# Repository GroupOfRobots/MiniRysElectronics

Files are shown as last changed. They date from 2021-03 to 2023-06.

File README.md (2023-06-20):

# MiniRysElectronics
This repo contains schematics and PCB layouts for all the custom boards used by the MiniRyś robot.

supervisor: Kamil Jabłoński

Boards:
* RysBoard
* RysBattery
* beacon (obsolete)
* dwm1000_addon (obsolete)

## RysBoard
Main board for the MiniRyś robot - a Raspberry Pi 4B shield with motor drivers, power delivery circuitry, sensor connectors and more.

## RysBattery
Custom 18650 battery holder supporting protected cells (longer!) and with reverse polarity protection.

## Beacon
(obsolete)

A STM Nucleo adapter for the DWM1000 module with a power input jack.

## DWM1000 addon
(obsolete)

A DWM1000 module breakout board that was to be compatible with both the RysBoard and the Beacon boards.

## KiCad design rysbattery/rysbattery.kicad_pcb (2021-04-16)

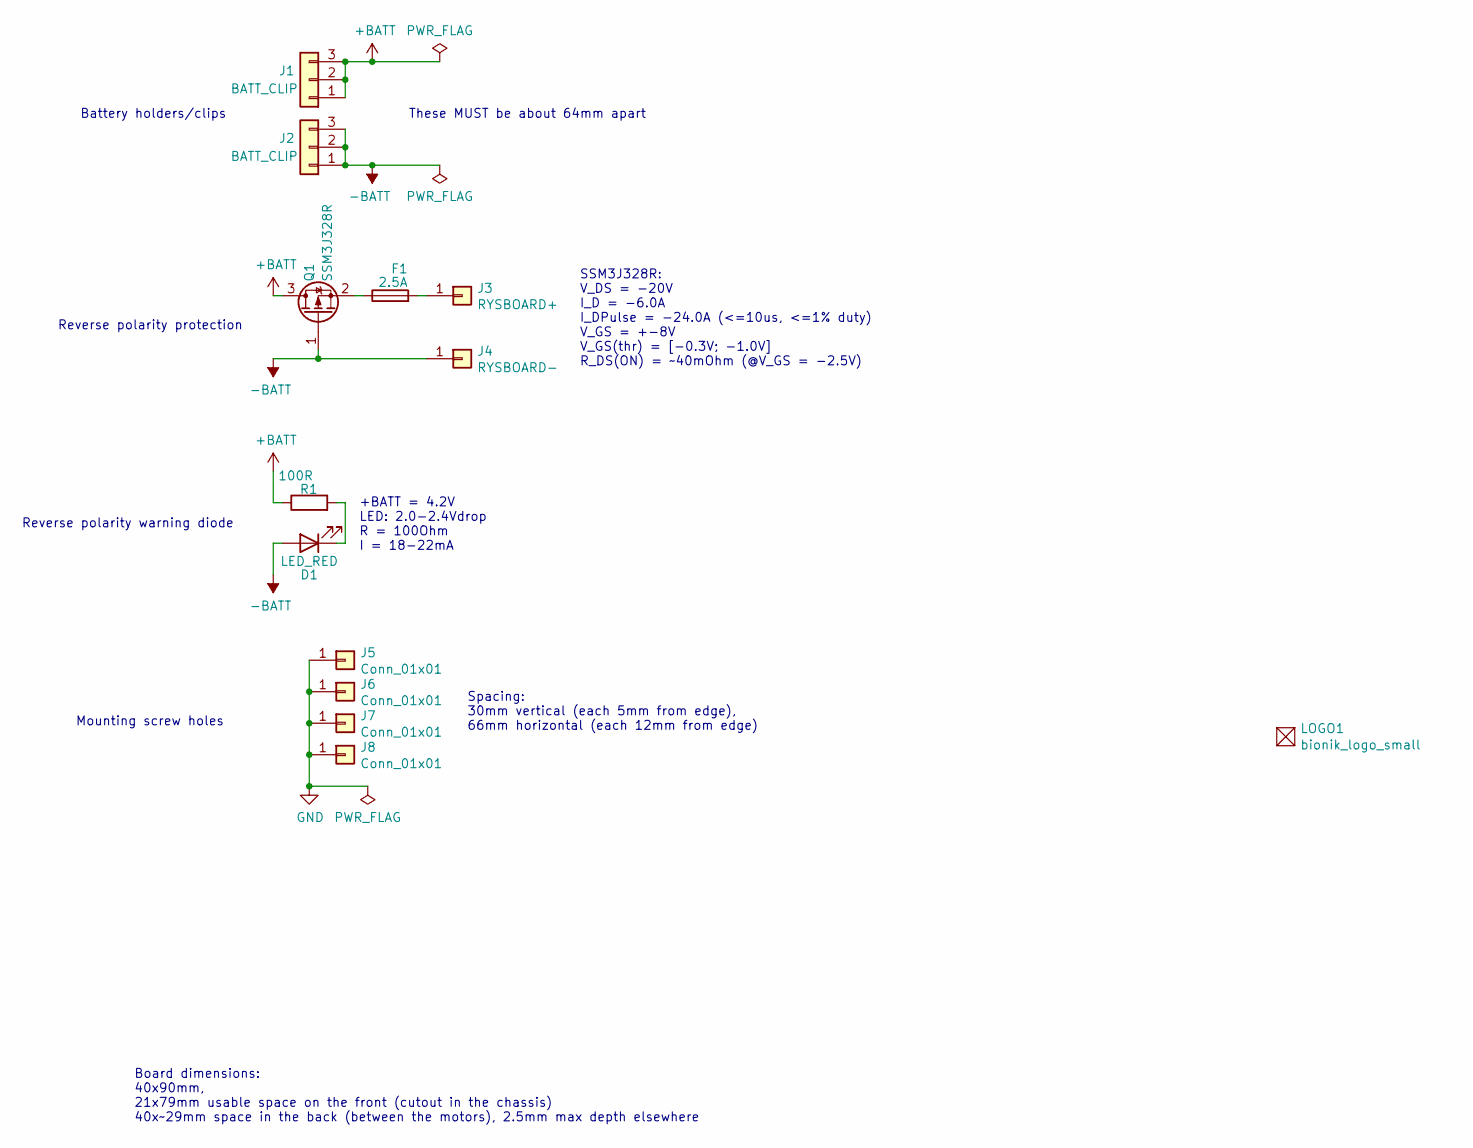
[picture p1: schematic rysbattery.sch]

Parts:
D1: LED_RED; LED_0805_2012Metric_Pad1.15x1.40mm_HandSolder
F1: 2.5A; Fuse_1206_3216Metric_Pad1.42x1.75mm_HandSolder
J1, J2: BATT_CLIP; keystone_54
J3: RYSBOARD+; SolderWire-0.75sqmm_1x01_D1.25mm_OD2.3mm_Relief
J4: RYSBOARD-; SolderWire-0.75sqmm_1x01_D1.25mm_OD2.3mm_Relief
J5, J6, J7, J8: Conn_01x01; MountingHole_3.2mm_M3_DIN965_Pad
LOGO1: bionik_logo_small
Q1: SSM3J328R; SOT-23_Handsoldering
R1: 100R; R_0603_1608Metric_Pad1.05x0.95mm_HandSolder

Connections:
+BATT: J1.1, J1.2, J1.3, Q1.3 (D), R1.1
-BATT: D1.2 (A), J2.1, J2.2, J2.3, J4.1, Q1.1 (G)
GND: J5.1, J6.1, J7.1, J8.1
unnamed: D1.1 (K), R1.2
unnamed: F1.1, Q1.2 (S)
unnamed: F1.2, J3.1

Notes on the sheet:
Reverse polarity warning diode
+BATT = 4.2V LED: 2.0-2.4Vdrop R = 100Ohm I = 18-22mA
Battery holders/clips
These MUST be about 64mm apart
Reverse polarity protection
Mounting screw holes
SSM3J328R: V_DS = -20V I_D = -6.0A I_DPulse = -24.0A (<=10us, <=1% duty) V_GS = +-8V V_GS(thr) = [-0.3V; -1.0V] R_DS(ON) = ~~40mOhm (@V_GS = -2.5V)
Spacing: 30mm vertical (each 5mm from edge), 66mm horizontal (each 12mm from edge)
Board dimensions: 40x90mm, 21x79mm usable space on the front (cutout in the chassis) 40x~~29mm space in the back (between the motors), 2.5mm max depth elsewhere

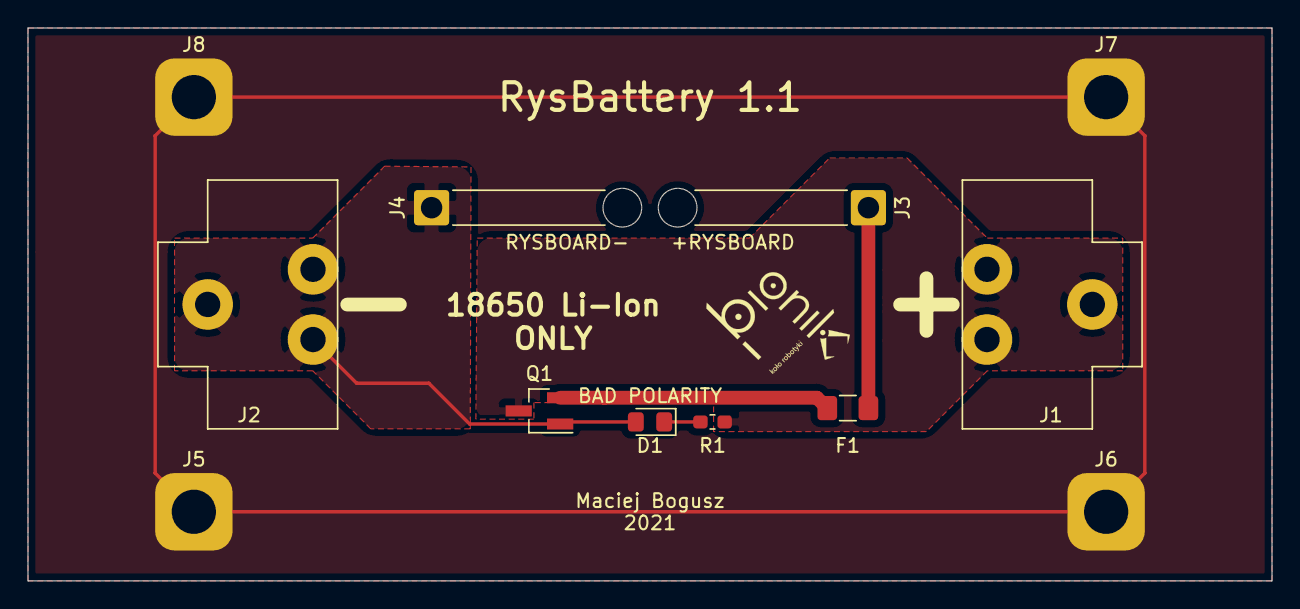
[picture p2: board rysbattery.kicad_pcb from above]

Board: 2 copper layers, 90.0 x 40.0 mm, 13 parts (0 on the bottom side), 6 nets.

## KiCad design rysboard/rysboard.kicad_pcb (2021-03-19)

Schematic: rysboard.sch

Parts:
D6: GREEN; LED_0805_2012Metric
D7: RED; LED_0805_2012Metric
D10: 1N4148; D_0603_1608Metric
H1, H2, H3, H4: MountingHole_Pad; MountingHole_2.7mm_M2.5_Pad
J1: RPi4; PinSocket_2x20_P2.54mm_Vertical
J17: Conn_01x03; PinHeader_1x03_P2.54mm_Vertical
J18: Conn_01x02; PinHeader_1x02_P2.54mm_Vertical
LOGO1: bionik_logo
Q1: BC847BS; SOT-363_SC-70-6
Q2: BC817; SOT-23
R7, R10: 10k; R_0603_1608Metric
R11, R12, R15: 680R; R_0603_1608Metric

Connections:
+3V3: J1.1 (3V3), J1.17 (3V3); also elsewhere on the board
+5V: D10.1, J1.2 (5V), J1.4 (5V), J18.2, R11.2, R12.1; also elsewhere on the board
/FAN_PWM: J1.12 (GPIO18/PWM0), R15.1
/I2C1_SCL: J1.5 (SCL/GPIO3); also elsewhere on the board
/I2C1_SDA: J1.3 (SDA/GPIO2); also elsewhere on the board
/I2C3_SCL: J1.29 (GCLK1/GPIO5); also elsewhere on the board
/I2C3_SDA: J1.7 (GCLK0/GPIO4); also elsewhere on the board
/I2C5_SCL: J1.33 (PWM1/GPIO13); also elsewhere on the board
/I2C5_SDA: J1.32 (PWM0/GPIO12); also elsewhere on the board
/LED1: J1.16 (GPIO23), R10.2
/LED2: J1.18 (GPIO24), R7.2
/MOTOR_BUSY: J1.13 (GPIO27); also elsewhere on the board
/MOTOR_FLAG: J1.11 (GPIO17); also elsewhere on the board
/SPI_CLK: J1.23 (SCLK0/GPIO11); also elsewhere on the board
/SPI_IRQEXT: J1.22 (GPIO25); also elsewhere on the board
/SPI_MISO: J1.21 (MISO0/GPIO9); also elsewhere on the board
/SPI_MOSI: J1.19 (MOSI0/GPIO10); also elsewhere on the board
/TOF1_EN: J1.31 (GCLK2/GPIO6); also elsewhere on the board
/TOF2_EN: J1.36 (GPIO16); also elsewhere on the board
/TOF3_EN: J1.35 (GPIO19/MISO1); also elsewhere on the board
/TOF4_EN: J1.38 (GPIO20/MOSI1); also elsewhere on the board
/TOF5_EN: J1.40 (GPIO21/SCLK1); also elsewhere on the board
/TOF6_EN: J1.37 (GPIO26); also elsewhere on the board
/UART_RXD: J1.10 (GPIO15/RXD), J17.3
/UART_TXD: J1.8 (GPIO14/TXD), J17.2
/~MOTOR_STBY: J1.15 (GPIO22); also elsewhere on the board
/~SPI_CS0: J1.24 (~CE0~/GPIO8); also elsewhere on the board
/~SPI_CS1: J1.26 (~CE1~/GPIO7); also elsewhere on the board
GND: H1.1, H2.1, H3.1, H4.1, J1.6 (GND), J1.9 (GND), J1.14 (GND), J1.20 (GND), J1.25 (GND), J1.30 (GND), J1.39 (GND), J17.1, Q1.1, Q1.4, Q2.2; also elsewhere on the board
unnamed: D6.1 (K), Q1.3
unnamed: D6.2 (A), R11.1
unnamed: D7.1 (K), Q1.6
unnamed: D7.2 (A), R12.2
unnamed: D10.2, J18.1, Q2.3
unnamed: Q1.2, R10.1
unnamed: Q1.5, R7.1
unnamed: Q2.1, R15.2

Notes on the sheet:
Raspberry Pi 4 connector
Status LEDs
UART connector
Raspberry Pi 4 mounting holes (GND)
I2C Note: RPi4 has internal pull-ups for I2C-1 bus and the ToF sensor boards used have a set of pull-ups each for their respective buses (I2C-3 and -5); Therefore no additional pullups are required
Cooling Fan

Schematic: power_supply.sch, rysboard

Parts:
C15, C18, C22: 100n; C_0603_1608Metric
C16, C17, C20, C21: 10u; C_1206_3216Metric
C19: 10n; C_0603_1608Metric
D3: RED; LED_0805_2012Metric
D4, D9: GREEN; LED_0805_2012Metric
D5, D8: SK52; D_SMB
F1: 2.5A; Fuse_1206_3216Metric
J4: CELL3; Molex_Micro-Fit_3.0_43045-0212_2x01_P3.00mm_Vertical
J5: CELL2; Molex_Micro-Fit_3.0_43045-0212_2x01_P3.00mm_Vertical
J6: CELL1; Molex_Micro-Fit_3.0_43045-0212_2x01_P3.00mm_Vertical
J7: SW; Molex_Micro-Fit_3.0_43045-0212_2x01_P3.00mm_Vertical
L1: 3.3uH; L_6.7x6.7_H2.2
R8, R9, R25: 10k; R_0603_1608Metric
R13: 110k1%; R_0603_1608Metric
R14: 21k1%; R_0603_1608Metric
R19: 15k1%; R_0603_1608Metric
R20, R22, R24: 10k1%; R_0603_1608Metric
R21: 36k1%; R_0603_1608Metric
R23: 56k1%; R_0603_1608Metric
R27: 680R; R_0603_1608Metric
U3: ST1S10; TI_SO-PowerPAD-8; PartID ST1S10PHR
U4: MAX11613; 8-uMAX; PartID MAX11613EUA+

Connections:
+3V3: C15.1, U4.8; also elsewhere on the board
+5V: C19.1, C20.1, C21.1, C22.1, D8.1 (K), D9.2 (A), R13.2; also elsewhere on the board
/I2C1_SCL: U4.5; also elsewhere on the board
/I2C1_SDA: U4.6; also elsewhere on the board
/Power Supply/V_CELL1: J5.1, J6.2, R19.1
/Power Supply/V_CELL2: J4.1, J5.2, R21.1
/Power Supply/V_CELL3: F1.2, J4.2, R8.2, R23.1
GND: C15.2, C16.2, C17.2, C18.2, C19.2, C20.2, C21.2, C22.2, J7.1, R9.2, R14.2, R20.1, R22.1, R24.1, R25.1, R27.2, U3.4 (AGND), U3.5 (SYNC), U3.8 (PGND), U3.9 (PADGND), U4.7; also elsewhere on the board
unnamed: D3.1 (K), D4.2 (A), D5.2 (A), F1.1
unnamed: D3.2 (A), R8.1
unnamed: D4.1 (K), R9.1
unnamed: D8.2 (A), L1.2
unnamed: D9.1 (K), R27.1
unnamed: J6.1, J7.2
unnamed: L1.1, U3.7 (SW)
unnamed: R13.1, R14.1, U3.3 (FB)
unnamed: R19.2, R20.2, U4.1
unnamed: R21.2, R22.2, U4.2
unnamed: R23.2, R24.2, U4.3
unnamed: R25.2, U4.4
Vdrive: C16.1, C17.1, C18.1, D5.1 (K), U3.1 (VINA), U3.2 (INH), U3.6 (VINSW); also elsewhere on the board

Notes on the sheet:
Step-down converter
I2C ADC
V_CELL1: 3.0 - 4.2V -> Div 2.5 V_CELL2: 6.0 - 8.4V -> Div 4.5 V_CELL3: 9.0 - 12.6V -> Div 6.5 V_REF: 2.048V
V_out = V_FB * (1 + R13/R14) R13 = R14 x (V_out - V_FB) / V_FB V_out ~= 5.0V V_FB = 0.8V (typ); +-24mV R14 = 21k & R13 = 110k -> V_out = 4.99V

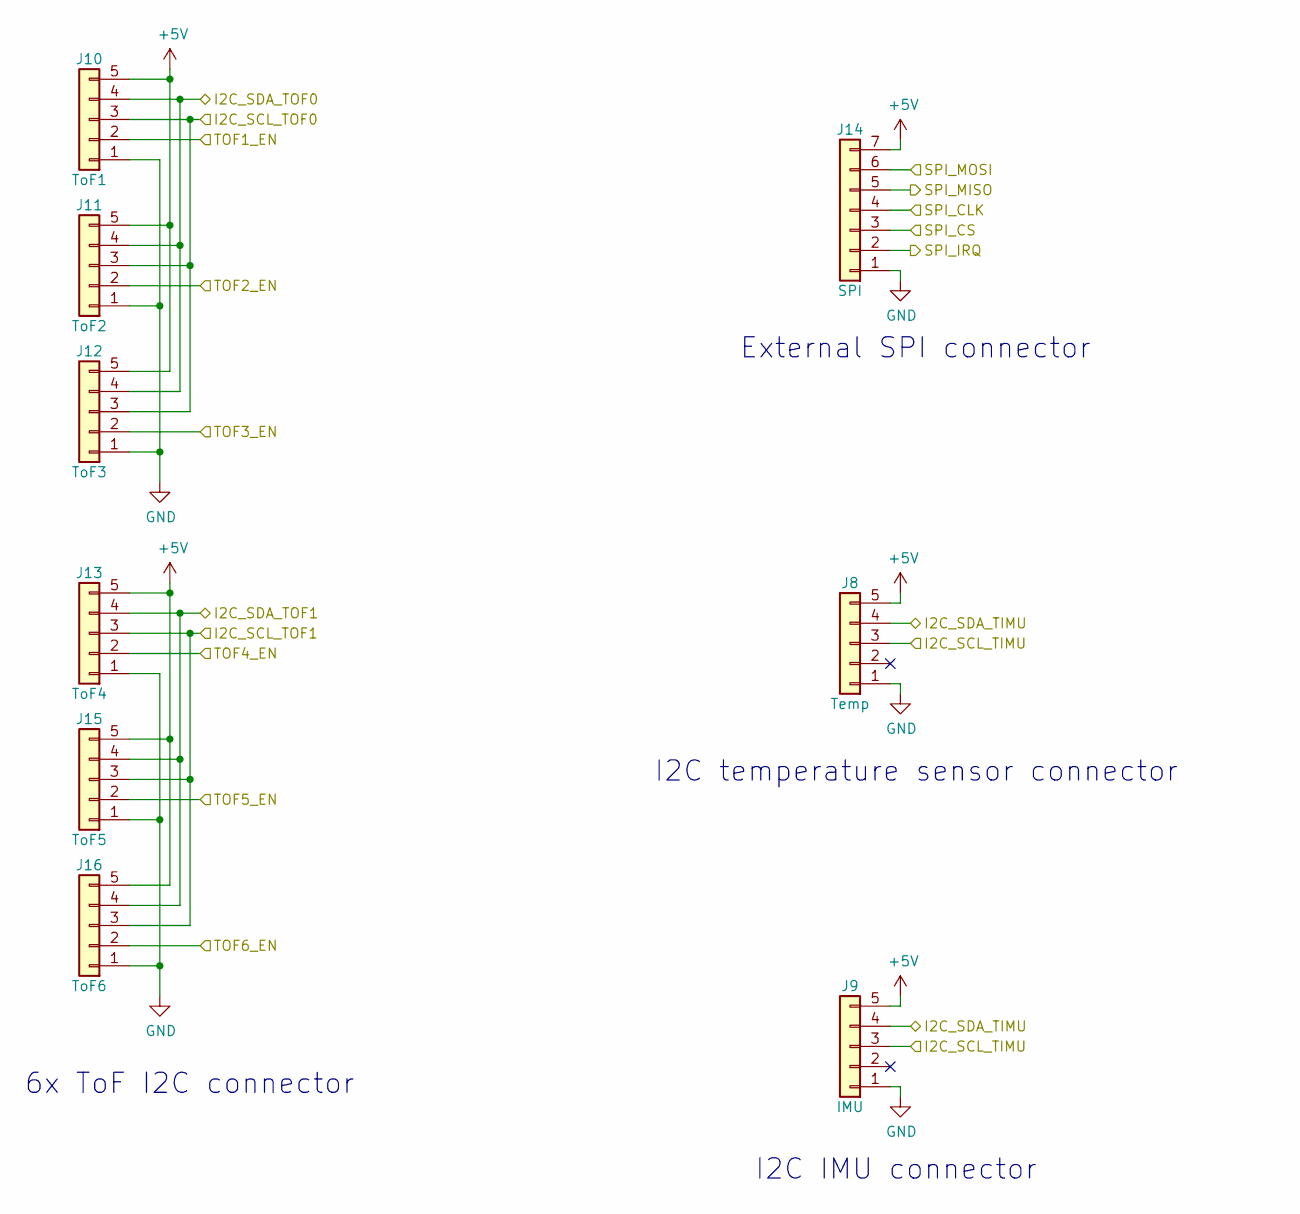
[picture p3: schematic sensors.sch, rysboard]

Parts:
J8: Temp; Molex_PicoBlade_53047-0510_1x05_P1.25mm_Vertical
J9: IMU; Molex_PicoBlade_53047-0510_1x05_P1.25mm_Vertical
J10: ToF1; Molex_PicoBlade_53047-0510_1x05_P1.25mm_Vertical
J11: ToF2; Molex_PicoBlade_53047-0510_1x05_P1.25mm_Vertical
J12: ToF3; Molex_PicoBlade_53047-0510_1x05_P1.25mm_Vertical
J13: ToF4; Molex_PicoBlade_53047-0510_1x05_P1.25mm_Vertical
J14: SPI; Molex_PicoBlade_53047-0710_1x07_P1.25mm_Vertical
J15: ToF5; Molex_PicoBlade_53047-0510_1x05_P1.25mm_Vertical
J16: ToF6; Molex_PicoBlade_53047-0510_1x05_P1.25mm_Vertical

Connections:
+5V: J8.5, J9.5, J10.5, J11.5, J12.5, J13.5, J14.7, J15.5, J16.5; also elsewhere on the board
/I2C1_SCL: J8.3, J9.3; also elsewhere on the board
/I2C1_SDA: J8.4, J9.4; also elsewhere on the board
/I2C3_SCL: J10.3, J11.3, J12.3; also elsewhere on the board
/I2C3_SDA: J10.4, J11.4, J12.4; also elsewhere on the board
/I2C5_SCL: J13.3, J15.3, J16.3; also elsewhere on the board
/I2C5_SDA: J13.4, J15.4, J16.4; also elsewhere on the board
/SPI_CLK: J14.4; also elsewhere on the board
/SPI_IRQEXT: J14.2; also elsewhere on the board
/SPI_MISO: J14.5; also elsewhere on the board
/SPI_MOSI: J14.6; also elsewhere on the board
/TOF1_EN: J10.2; also elsewhere on the board
/TOF2_EN: J11.2; also elsewhere on the board
/TOF3_EN: J12.2; also elsewhere on the board
/TOF4_EN: J13.2; also elsewhere on the board
/TOF5_EN: J15.2; also elsewhere on the board
/TOF6_EN: J16.2; also elsewhere on the board
/~SPI_CS1: J14.3; also elsewhere on the board
GND: J8.1, J9.1, J10.1, J11.1, J12.1, J13.1, J14.1, J15.1, J16.1; also elsewhere on the board

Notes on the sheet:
External SPI connector
I2C temperature sensor connector
6x ToF I2C connector
I2C IMU connector

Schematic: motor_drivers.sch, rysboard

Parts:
C1, C8: 10u; C_1206_3216Metric
C2, C9: 220n; C_0805_2012Metric
C3, C10: 10n; C_0603_1608Metric
C4, C7, C11, C14: 100n; C_0603_1608Metric
C5, C6, C12, C13: 47u; CP_EIA-7343-31_Kemet-D
D1, D2: BAV99; SOT-23
J2: Motor L; Molex_Micro-Fit_3.0_43650-0415_1x04_P3.00mm_Vertical
J3: Motor R; Molex_Micro-Fit_3.0_43650-0415_1x04_P3.00mm_Vertical
R1, R2, R26: 10k; R_0603_1608Metric
R3, R5: 27k1%; R_0603_1608Metric
R4, R6: 10k1%; R_0603_1608Metric
U1, U2: L6470; HTSSOP-28-1EP_4.4x9.7mm_P0.65mm_EP3.4x9.5mm_ThermalVias

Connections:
+3V3: C1.1, C4.1, C8.1, C11.1, R1.1, R2.1, R26.1, U1.4 (SW), U1.6 (VREG), U1.17 (VDD), U2.4 (SW), U2.6 (VREG), U2.17 (VDD); also elsewhere on the board
/Motor Drivers/SPI_BRIDGE: U1.18 (SDO), U2.20 (SDI)
/Motor Drivers/~BUSY_1: R2.2, U1.22 (~BUSY~/SYNC); also elsewhere on the board
/Motor Drivers/~BUSY_2: R26.2, U2.22 (~BUSY~/SYNC); also elsewhere on the board
/Motor Drivers/~FLAG_1: U1.24 (~FLAG); also elsewhere on the board
/Motor Drivers/~FLAG_2: U2.24 (~FLAG); also elsewhere on the board
/SPI_CLK: U1.19 (SCLK), U2.19 (SCLK); also elsewhere on the board
/SPI_MISO: U2.18 (SDO); also elsewhere on the board
/SPI_MOSI: U1.20 (SDI); also elsewhere on the board
/~MOTOR_STBY: R1.2, U1.3 (~STBY~/~RST), U2.3 (~STBY~/~RST); also elsewhere on the board
/~SPI_CS0: U1.23 (~CS), U2.23 (~CS); also elsewhere on the board
GND: C1.2, C4.2, C5.2, C6.2, C7.2, C8.2, C11.2, C12.2, C13.2, C14.2, R4.2, R6.2, U1.9 (AGND), U1.13 (PGND), U1.21 (DGND), U1.27 (PGND), U1.29 (GND), U2.9 (AGND), U2.13 (PGND), U2.21 (DGND), U2.27 (PGND), U2.29 (GND); also elsewhere on the board
unnamed: C2.2, D1.2 (A), U1.11 (VBOOT)
unnamed: C3.1, D1.3 (K)
unnamed: C3.2, U1.10 (CP)
unnamed: C9.2, D2.2 (A), U2.11 (VBOOT)
unnamed: C10.1, D2.3 (K)
unnamed: C10.2, U2.10 (CP)
unnamed: J2.1, U1.28 (OUT2A)
unnamed: J2.2, U1.1 (OUT1A)
unnamed: J2.3, U1.14 (OUT1B)
unnamed: J2.4, U1.15 (OUT2B)
unnamed: J3.1, U2.28 (OUT2A)
unnamed: J3.2, U2.1 (OUT1A)
unnamed: J3.3, U2.14 (OUT1B)
unnamed: J3.4, U2.15 (OUT2B)
unnamed: R3.2, R4.1, U1.5 (ADCIN)
unnamed: R5.2, R6.1, U2.5 (ADCIN)
Vdrive: C2.1, C5.1, C6.1, C7.1, C9.1, C12.1, C13.1, C14.1, D1.1 (K), D2.1 (K), R3.1, R5.1, U1.2 (VSA), U1.12 (VSB), U1.16 (VSB), U1.26 (VSA), U2.2 (VSA), U2.12 (VSB), U2.16 (VSB), U2.26 (VSA); also elsewhere on the board

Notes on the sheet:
Pull-ups for STANDBY and BUSY flags (active low)

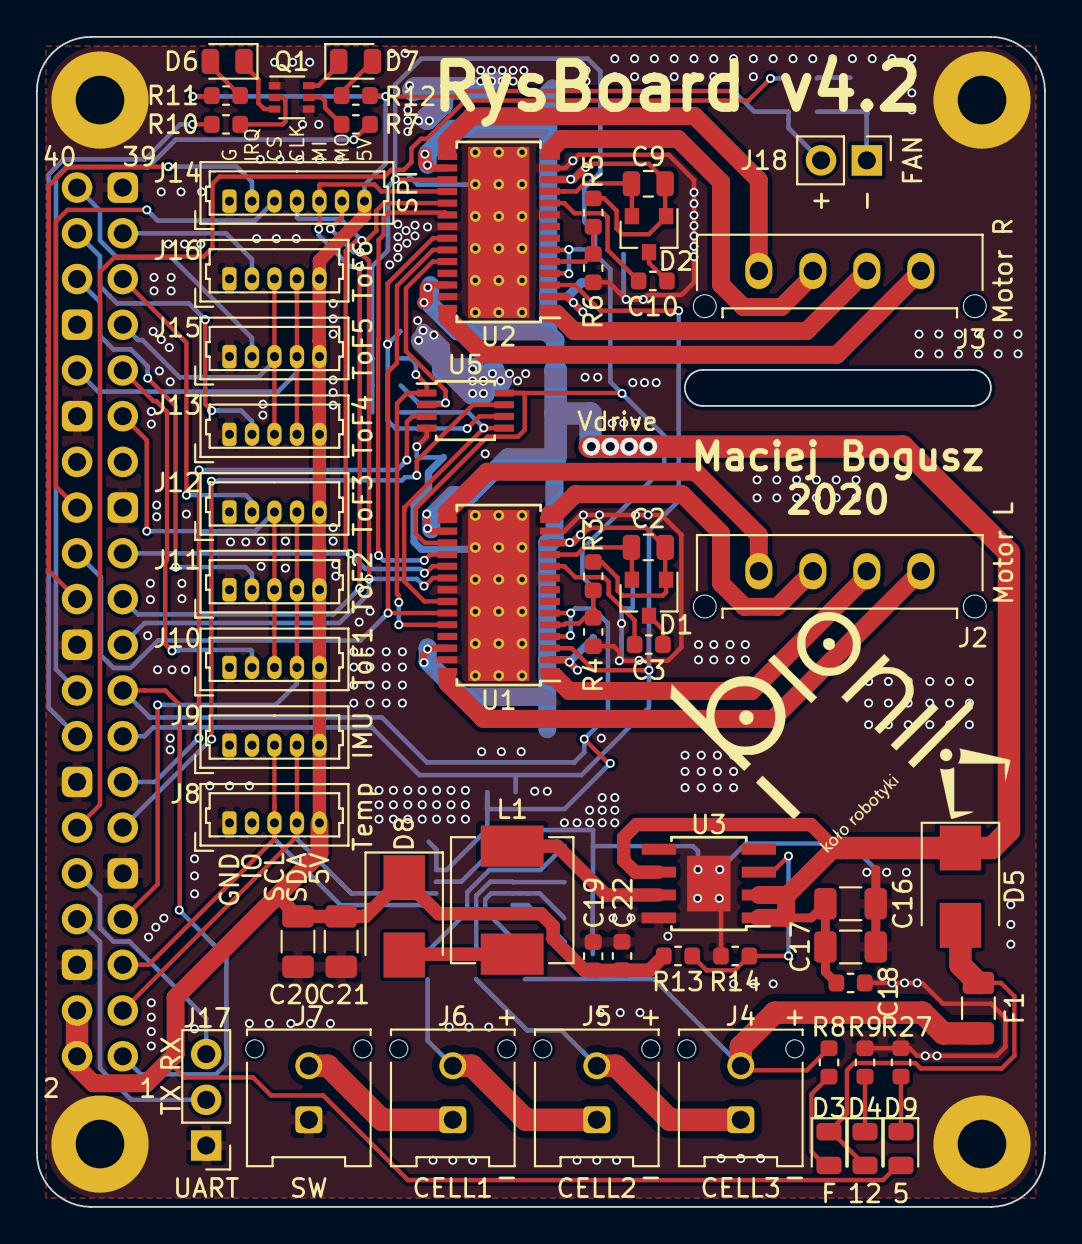
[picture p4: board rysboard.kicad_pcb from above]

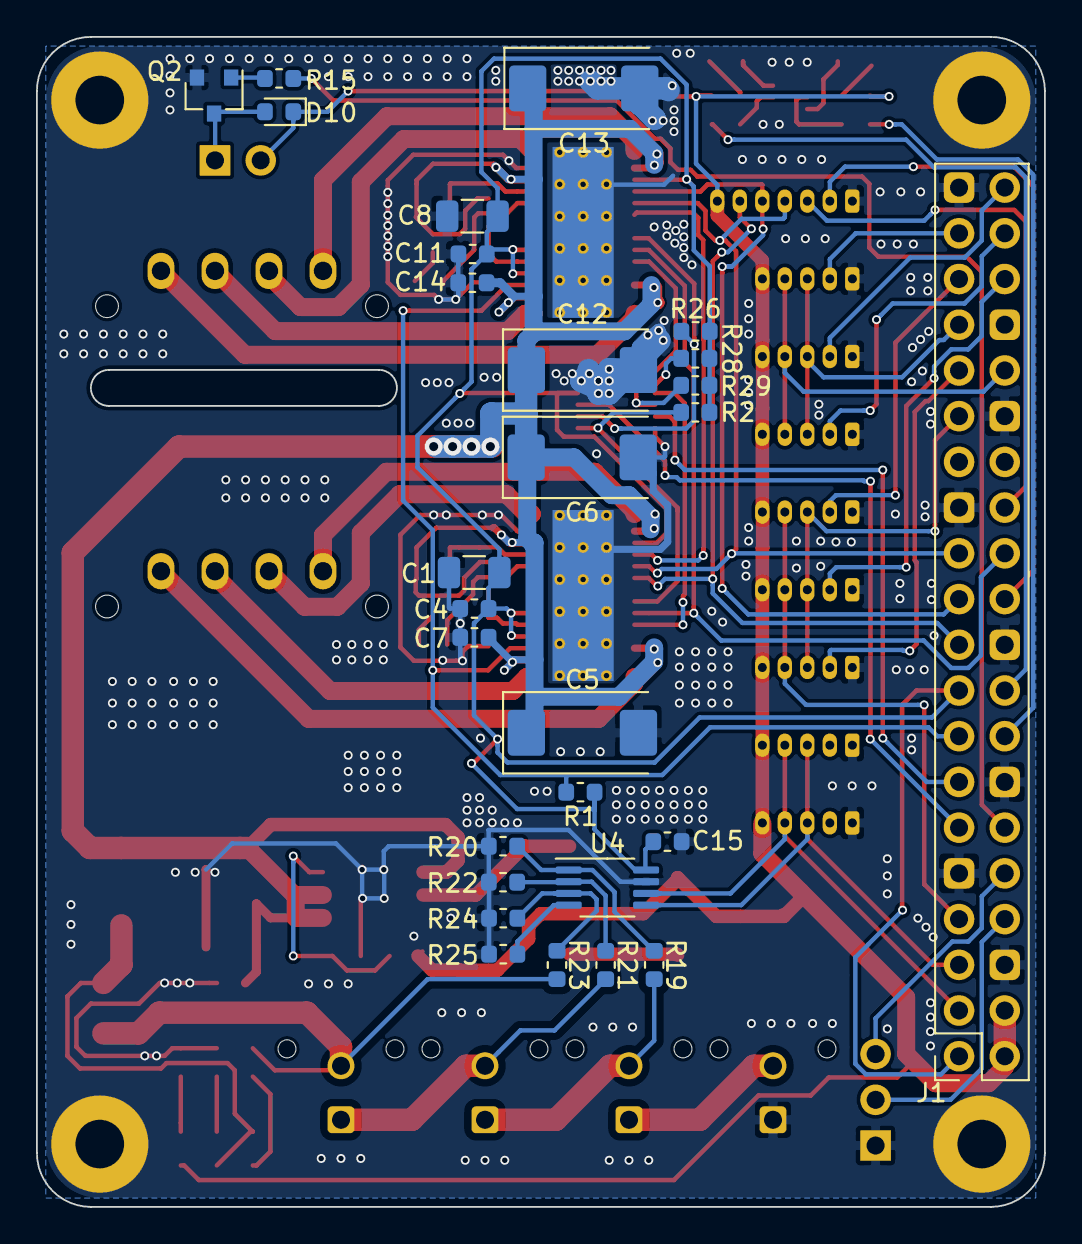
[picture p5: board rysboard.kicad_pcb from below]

Board: 2 copper layers, 56.0 x 65.0 mm, 90 parts (28 on the bottom side), 74 nets.

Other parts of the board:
R28, R29: 40k; R_0603_1608Metric
U5: 74HC2G00; TSSOP-8_3x3mm_P0.65mm

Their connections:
+3V3: R28.1, R29.1, U5.8; also elsewhere on the board
/MOTOR_BUSY: U5.3; also elsewhere on the board
/MOTOR_FLAG: U5.7; also elsewhere on the board
/Motor Drivers/~BUSY_1: U5.5; also elsewhere on the board
/Motor Drivers/~BUSY_2: U5.6; also elsewhere on the board
/Motor Drivers/~FLAG_1: R28.2, U5.1; also elsewhere on the board
/Motor Drivers/~FLAG_2: R29.2, U5.2; also elsewhere on the board
GND: U5.4; also elsewhere on the board

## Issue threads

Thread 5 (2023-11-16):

Badania nad ulepszeniem sterownika silników

jab3onski, 2023-11-16:
Planowana zmiana dotychczasowego sterownika silników krokowych L6470 na "świeży" model dla ulepszenia sprawności układu (zmniejszenie temperatur) i jakości kontroli silników

jab3onski, 2024-10-25:
Dobrym kandydatem jest [TMC2209](https://www.mouser.pl/datasheet/2/609/TMC2209_datasheet_rev1_09-3365120.pdf) programowanie przez UART, dobre zabezpieczenia i lepsze zarządzanie mocą - trzeba by porównać.
Dostępny na Botland: https://botland.com.pl/stepstick-sterowniki-do-silnikow-krokowych/19883-sterownik-silnika-krokowego-bigtreetech-tmc2209-v13-5904422379667.html

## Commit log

2016-03-28 nie chce misie
    [main.sch]
2016-03-31 initial board elements
    [dwm1000.sch, imu.sch, main.kicad_pcb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]
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2016-05-11 useful mods
    [mainboard.brd, mainboard.sch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]
2016-06-19 starting new version
    [beagleboard.brd, beagleboard.sch, mainboard.brd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]
2016-08-21 main wires
    [beagleboard.brd, beagleboard.sch]
2016-08-24 boardv2 ready to check
    [beagleboard.brd, beagleboard.sch]
2016-08-30 check pinout
    [beagleboard.brd]
2016-09-13 added distance sensor connectors
    [beagleboard.brd, beagleboard.sch]
2016-10-28 check and reconfigure gpios
    [beagleboard.brd, beagleboard.sch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]
2016-11-01 pin recinfiguration started
    [beagleboard.brd, beagleboard.sch]
2016-11-06 new gpio routed started
    [beagleboard.brd, beagleboard.sch]
2016-11-07 before logo
    [beagleboard.brd]
2016-12-11 right sonar wires
    [beagleboard.brd, beagleboard.sch]
2017-06-17 board 3.1: * zmienione szyny I2C1->I2C2, SPI1->SPI0 * poprawione dzielniki napięcia baterii * dodany dzielnik napięcia czujnika temperatury * poprawione etykiety i rozmieszczenie elementów na schemac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
    [beagleboard.brd, beagleboard.sch]
2017-06-20 board v3.1 beta 5: przepięte 2 TOF i MEN,M0,M1,M2, usunięte rezystory z tych linii, rerouting
    [beagleboard.brd, beagleboard.sch]
2017-06-21 gerber files, board report
    [b.gbl, bs.gbs, t.gtl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]
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2017-06-21 board v3.1 beta 6: poprawione dzielniki napięcia baterii na płytce
    [beagleboard.brd, beagleboard.sch]
2017-06-23 board v3.1 beta 6: poprawiony minimalny rozmiar otworu (DRC)
    [beagleboard.brd]
2017-06-28 dwm1000_addon: mini-płytka na moduł dwm1000 wpinana na złącze goldpin
    [dwm1000addon.brd, dwm1000addon.sch]
2017-07-07 dwm1000_addon: poprawione prowadzenie ścieżek masy
    [dwm1000addon.brd]
2017-07-07 board v3.1 beta 6: poprawione acid-trap przy dzielnikach napięcia baterii
    [beagleboard.brd]
2017-07-07 board v3.1 beta 7: replaced DWM1000 module with connector for dwm1000-addon board, redone battery cell voltage routes. No more vias.
    [beagleboard.brd, beagleboard.sch]
2017-07-07 board v3.1 beta 7: fixed bad networks between motor drivers and connectors; fixed some clearance issues
    [beagleboard.brd, beagleboard.sch]
2017-07-07 beacon: import płytki latarni lokalizacyjnej z repo RobotLocalization; rev 1.1: dwm1000 zastąpiony złączem na dwm1000-addon
    [mainboard.brd, mainboard.sch]
2017-07-20 dwm1000_addon: zmniejszone pole masy pod anteną, przesunięte diody aktywności
    [dwm1000addon.brd]
2017-07-31 gitignore: gerbery dodane do ignorowanych
    [b.gbl, bs.gbs, t.gtl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]
2017-07-31 latarnia (beacon): zmniejszone wymiary płytki
    [mainboard.brd]
2017-07-31 dwm1000 addon: dodane pola masy
    [dwm1000addon.brd, dwm1000addon.sch]
2017-08-01 dodane wymiary zewnętrzne płytek
    [beagleboard.brd, dwm1000addon.brd, mainboard.brd]
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2017-12-13 board3.1: updated resistors on voltage divider for power
    [beagleboard.brd, beagleboard.sch]
2018-03-03 v4 init
    [47351.stp, Encoder_Baord.SchDoc, Encoder_Board.PrjPcb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]
2018-07-19 battery pcb model
    [Battery_module.PrjPCB, battery_module.PcbDoc, battery_module.SchDoc]
2018-08-07 pico blade connectors
    [PicoBlade.PcbLib, PicoBlade.SchLib, Rys_PCB.PrjPcb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]
2018-10-17 raspberry layout
    [47351.stp, Battery_module.PrjPCB, Encoder_Baord.SchDoc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]
2018-10-18 power button
    [rys_PCB.SchDoc]
2018-10-21 battery module
    [Battery_module.PrjPCB, Rys_PCB.PrjPcb, battery_module.PcbDoc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]
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2018-11-29 board adjustments on PCB
    [Rys_PCB.PrjPcb, rys_PCB.PcbDoc, rys_PCB.SchDoc]
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2019-03-02 clean up repo and add TODO task
    [Battery_module.PrjPCB, Rys_PCB.PrjPcb, battery_module.PcbDoc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]
2019-03-02 improved battery module pads
    [Battery_module.PrjPCB, battery_module.PcbDoc, battery_module.SchDoc]
2019-03-17 voltage devider fix
    [Rys_PCB.PrjPcb, rys_PCB.SchDoc]
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2021-03-19 remove old versions (existing in git history)
    [beagleboard.brd, beagleboard.sch, dwm1000addon.brd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]
2021-03-19 rysboard: converted to kicad (initial version)
    [Rys_PCB.PrjPcb, rys_PCB.PcbDoc, rys_PCB.SchDoc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]
2021-03-19 rysboard: rpi4 connector and power supply cleaned up after import; clean up library and gitignore file
    [motor_drivers.sch, power_supply.sch, rysboard.kicad_pcb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]
2021-03-19 rysboard: schematic cleanup done after kicad import
    [motor_drivers.sch, power_supply.sch, rysboard.sch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]
2021-03-19 rysboard: library cleanup, fix bad connector references
    [motor_drivers.sch, power_supply.sch]
2021-03-19 rysboard: 4.2 schematic
    Change the I2C buses and GPIOs used
    Fix L6470 connections
    Change ADC to 4-channel
    Add 2 user LEDs
    Add I2C pullups
    Add serial connector
    [motor_drivers.sch, power_supply.sch, rysboard.sch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]
2021-03-19 rysboard: 4.2 schematic imported to pcb, initial version
    [rysboard.kicad_pcb]
2021-03-19 rysboard 4.2: * add converter output protection (shottky, D8) * fix converter resistor values (R13/R14) * add 5Vgood LED (D9) * add PWR_FLAGs for KiCAD's ERC * add NAND for motor driver's output flag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
    [motor_drivers.sch, power_supply.sch, rysboard.sch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]
2021-03-19 rysboard v4.2: * route the whole board (TODO: ground fills, track width checks) * fix half of ToF connectors missing ground connection * swap LEDs for easier routing
    [motor_drivers.sch, power_supply.sch, rysboard.kicad_pcb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]
2021-03-19 rysboard v4.2: adjust placement of text on pcb front side silkscreen
    [rysboard.kicad_pcb]
2021-03-19 rysboard v4.2: * re-add mountting holes * fix some layout errors * add ground fills * ensure proper track width * add front-side filkscreen
    [rysboard.kicad_pcb, rysboard.sch]
2021-03-19 rysboard v4.2: adjust silkscreen text positions, add board name, minor layout improvements
    [rysboard.kicad_pcb]
2021-03-19 rysboard v4.2: custom 6.7x6.7mm inductor footprint&model
    [power_supply.sch]
2021-03-19 rysboard v4.2: status LED transistor swapped for BC847BS; PCB design fixes after review (!1)
    [rysboard.kicad_pcb, rysboard.sch]
2021-03-19 rysboard: remove additional i2c pullups; increase high-voltage track clearance
    [rysboard.kicad_pcb, rysboard.sch]
2021-03-19 rysboard: changed LED and sensors' VCC to 5V
    [motor_drivers.sch, power_supply.sch, rysboard.kicad_pcb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]
2021-03-19 rysboard: move spi external interrupt line further from the edge
    [rysboard.kicad_pcb]
2021-03-19 rysboard: fix pour between SMD pins, fix acid pits, add +/- labels to battery connectors and Vdrive test point/area
    [rysboard.kicad_pcb]
2021-03-19 rysboard: fix additional acid pits, C15 cap placement, text orientation, added BIONIK logo and external SPI connector pinout
    [rysboard.kicad_pcb]
2021-03-19 rysboard: add missing molex 3d models
    [rysboard.kicad_pcb]
2021-03-19 rysboard: add PWM fan output
    [motor_drivers.sch, power_supply.sch, rysboard.kicad_pcb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]
2021-03-19 rysboard: move the camera ribbon slot closer to the port on the Pi
    [rysboard.kicad_pcb]
2021-03-19 rysboard: fix leftover acid pits
    [rysboard.kicad_pcb]
2021-03-19 rysboard: move D8 before converter feedback; replace U5 with counterpart of higher availability; fix U4 wiring; improve GND connections to motor drivers
    [motor_drivers.sch, power_supply.sch, rysboard.kicad_pcb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]
2021-03-19 rysboard: add missing BIONIK logo on silkscreen front
    [rysboard.kicad_pcb]
2021-03-19 rysboard: add BIONIK logo to schematic (to prevent it disappearing from PCB after every update)
    [rysboard.kicad_pcb, rysboard.sch]
2021-03-19 rysboard: fix BIONIK logo, fix ADC footprint, final version (sent to mfg)
    [power_supply.sch, rysboard.kicad_pcb, rysboard.sch]
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2021-04-16 rysbattery: remove old version (remains in git history)
    [Battery_module.PrjPCB, battery_module.PcbDoc, battery_module.SchDoc]
